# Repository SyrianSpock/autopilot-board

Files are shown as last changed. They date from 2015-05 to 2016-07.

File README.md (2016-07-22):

Speedy, the nanocopter
======================

The aim of this project is to design a board enabling the control of a small quadrotor (nanocopter) that can be tracked by external visual sensors.

### Specifications
* Cortex M4 MCU
* Four infrared LEDs on each side of the board for IR vision tracking. Each side can be controlled separately.
* Two full H bridges: one half bridge per motor to allow active braking of the motors.
* IMU:
    - MPU9250 (9 axis): accelerometer, gyroscope and magnetometer
    - MS5611 barometer
* Ground distance sensor:
    - ST VL53L0X for landing / ground approach
* Telemetry module:
    - ESP12E for telemetry and telecommand through WiFi
* USB interface (for DFU programming / serial interface) and power/charging
* Battery management unit
	- Monitor battery (current, voltage)
	- Supply power to the board from a LiPo (1S) input
	- Recharge the battery through USB

### PCB

The 40mm x 40mm board is rendered below
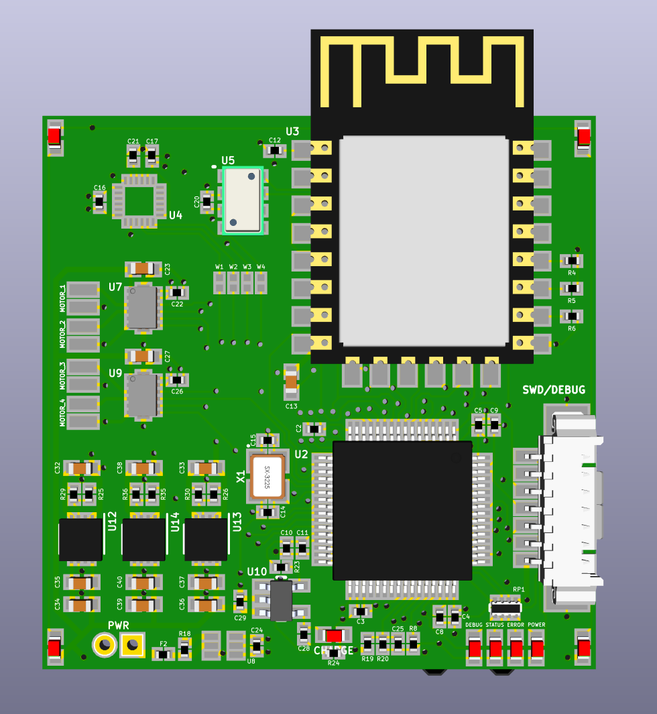
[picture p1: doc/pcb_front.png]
PCB front view

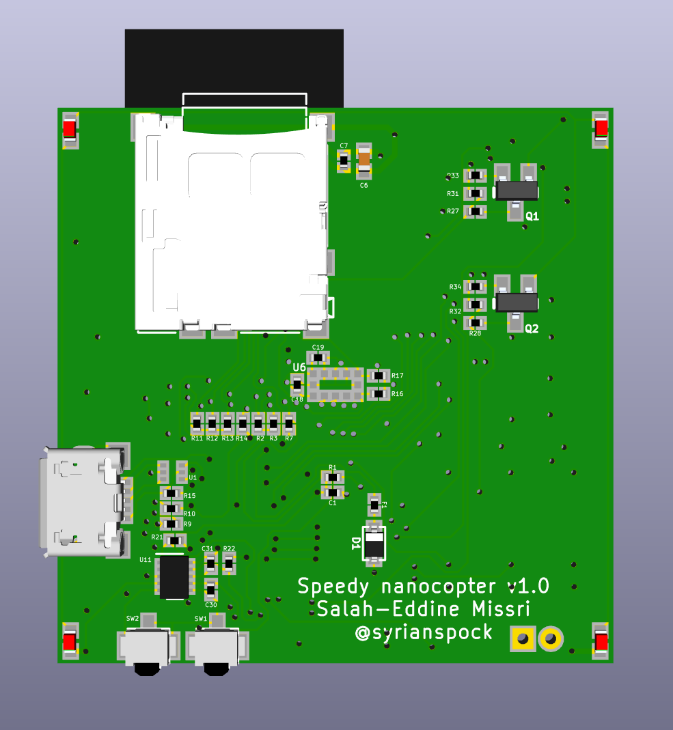
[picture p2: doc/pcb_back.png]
PCB back view


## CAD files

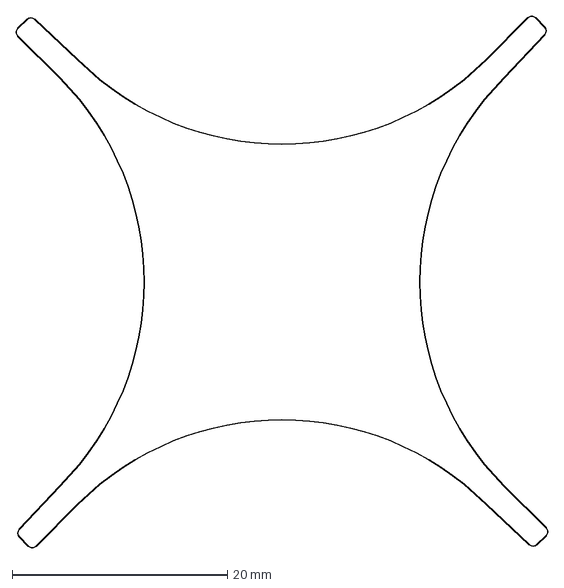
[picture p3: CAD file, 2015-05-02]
mechanics/PCB_shape.dxf
49.4 x 49.4 mm

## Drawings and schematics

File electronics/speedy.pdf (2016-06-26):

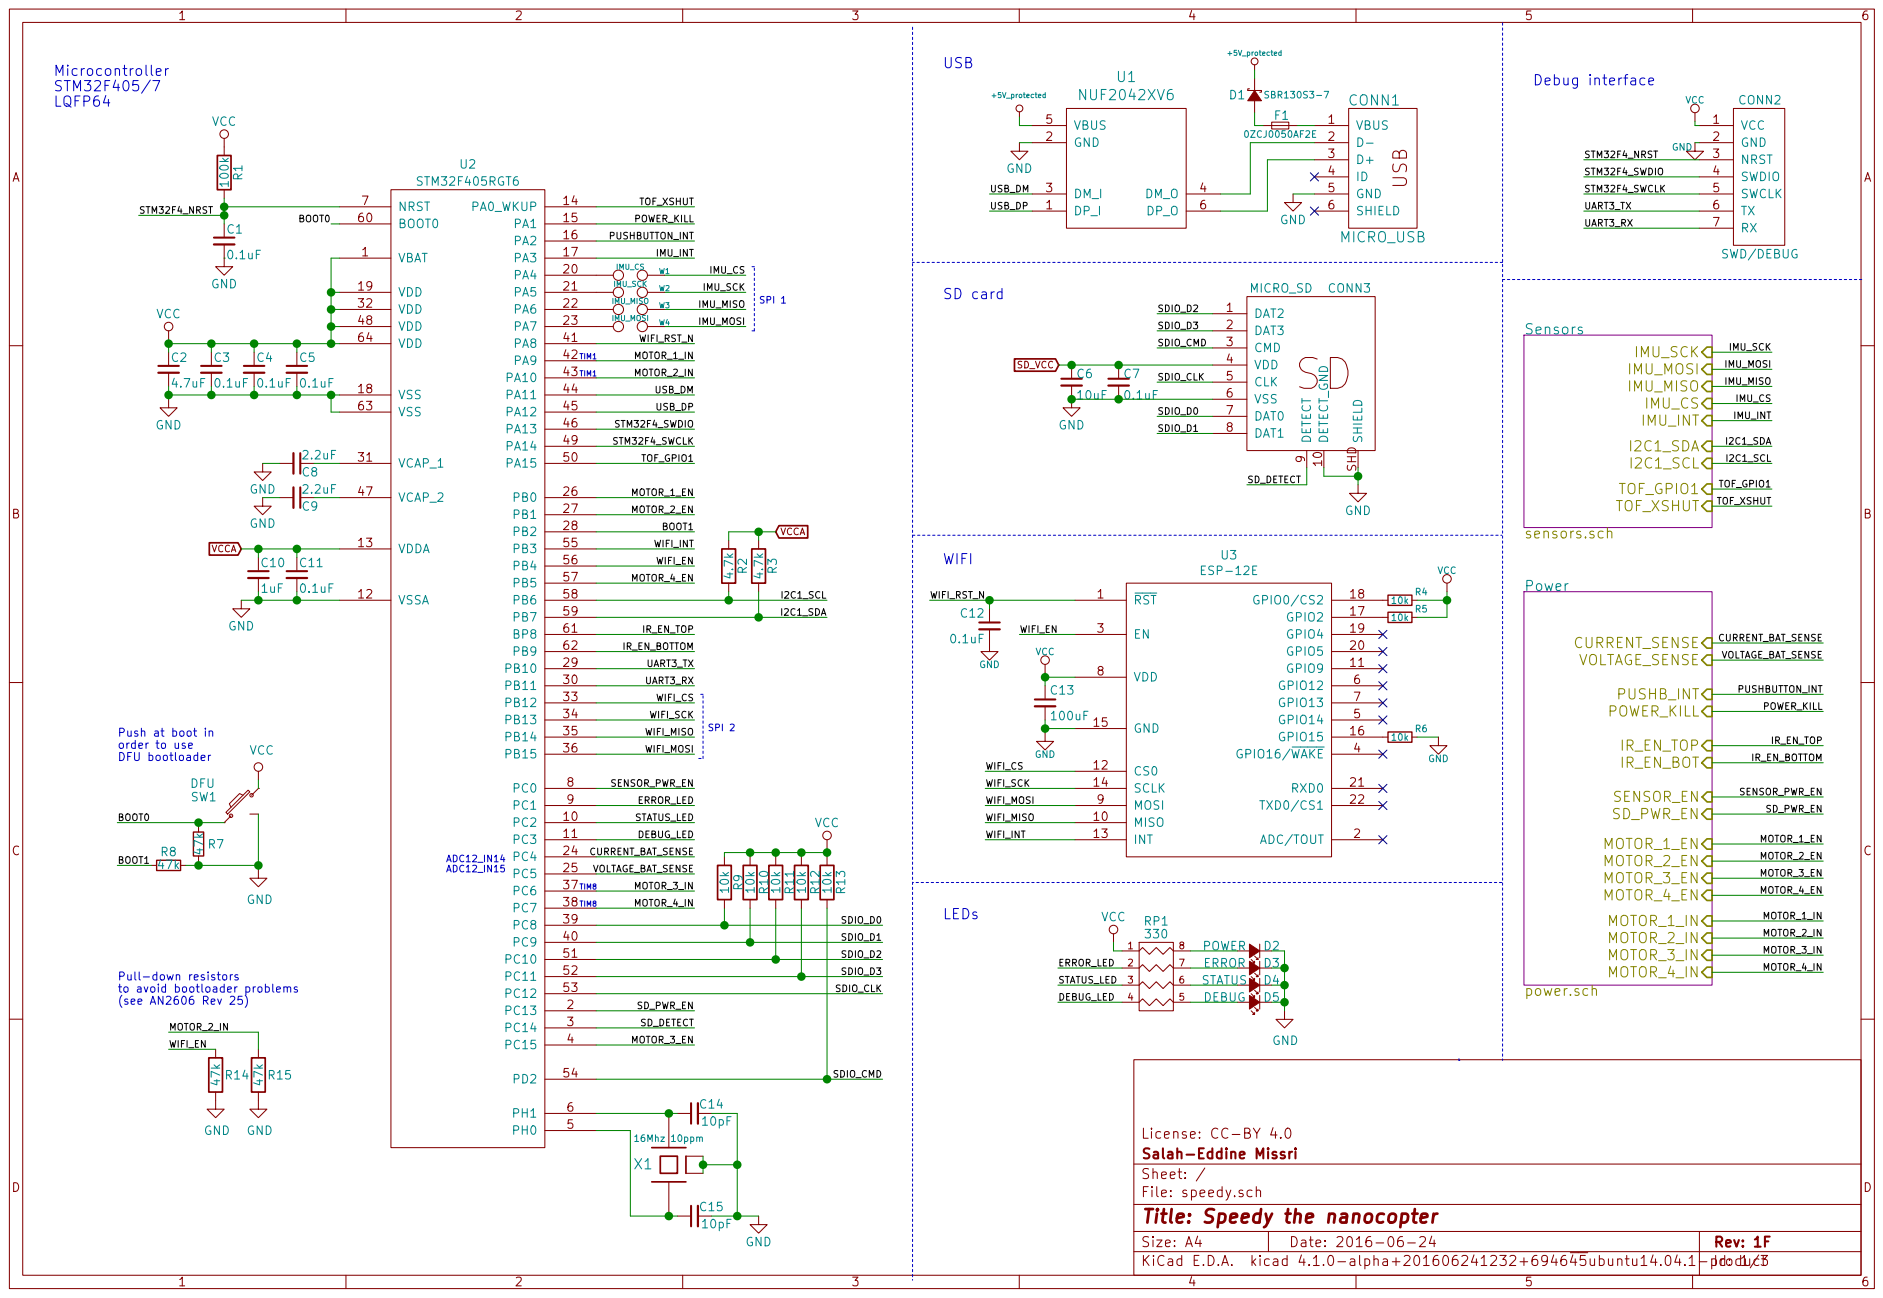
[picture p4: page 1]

Pull-down resistors
to avoid bootloader problems (see AN2606 Rev 25)

File: speedy.sch Sheet: / Salah-Eddine Missri License: CC-BY 4.0

Id: 1/3 Title: Speedy the nanocopter

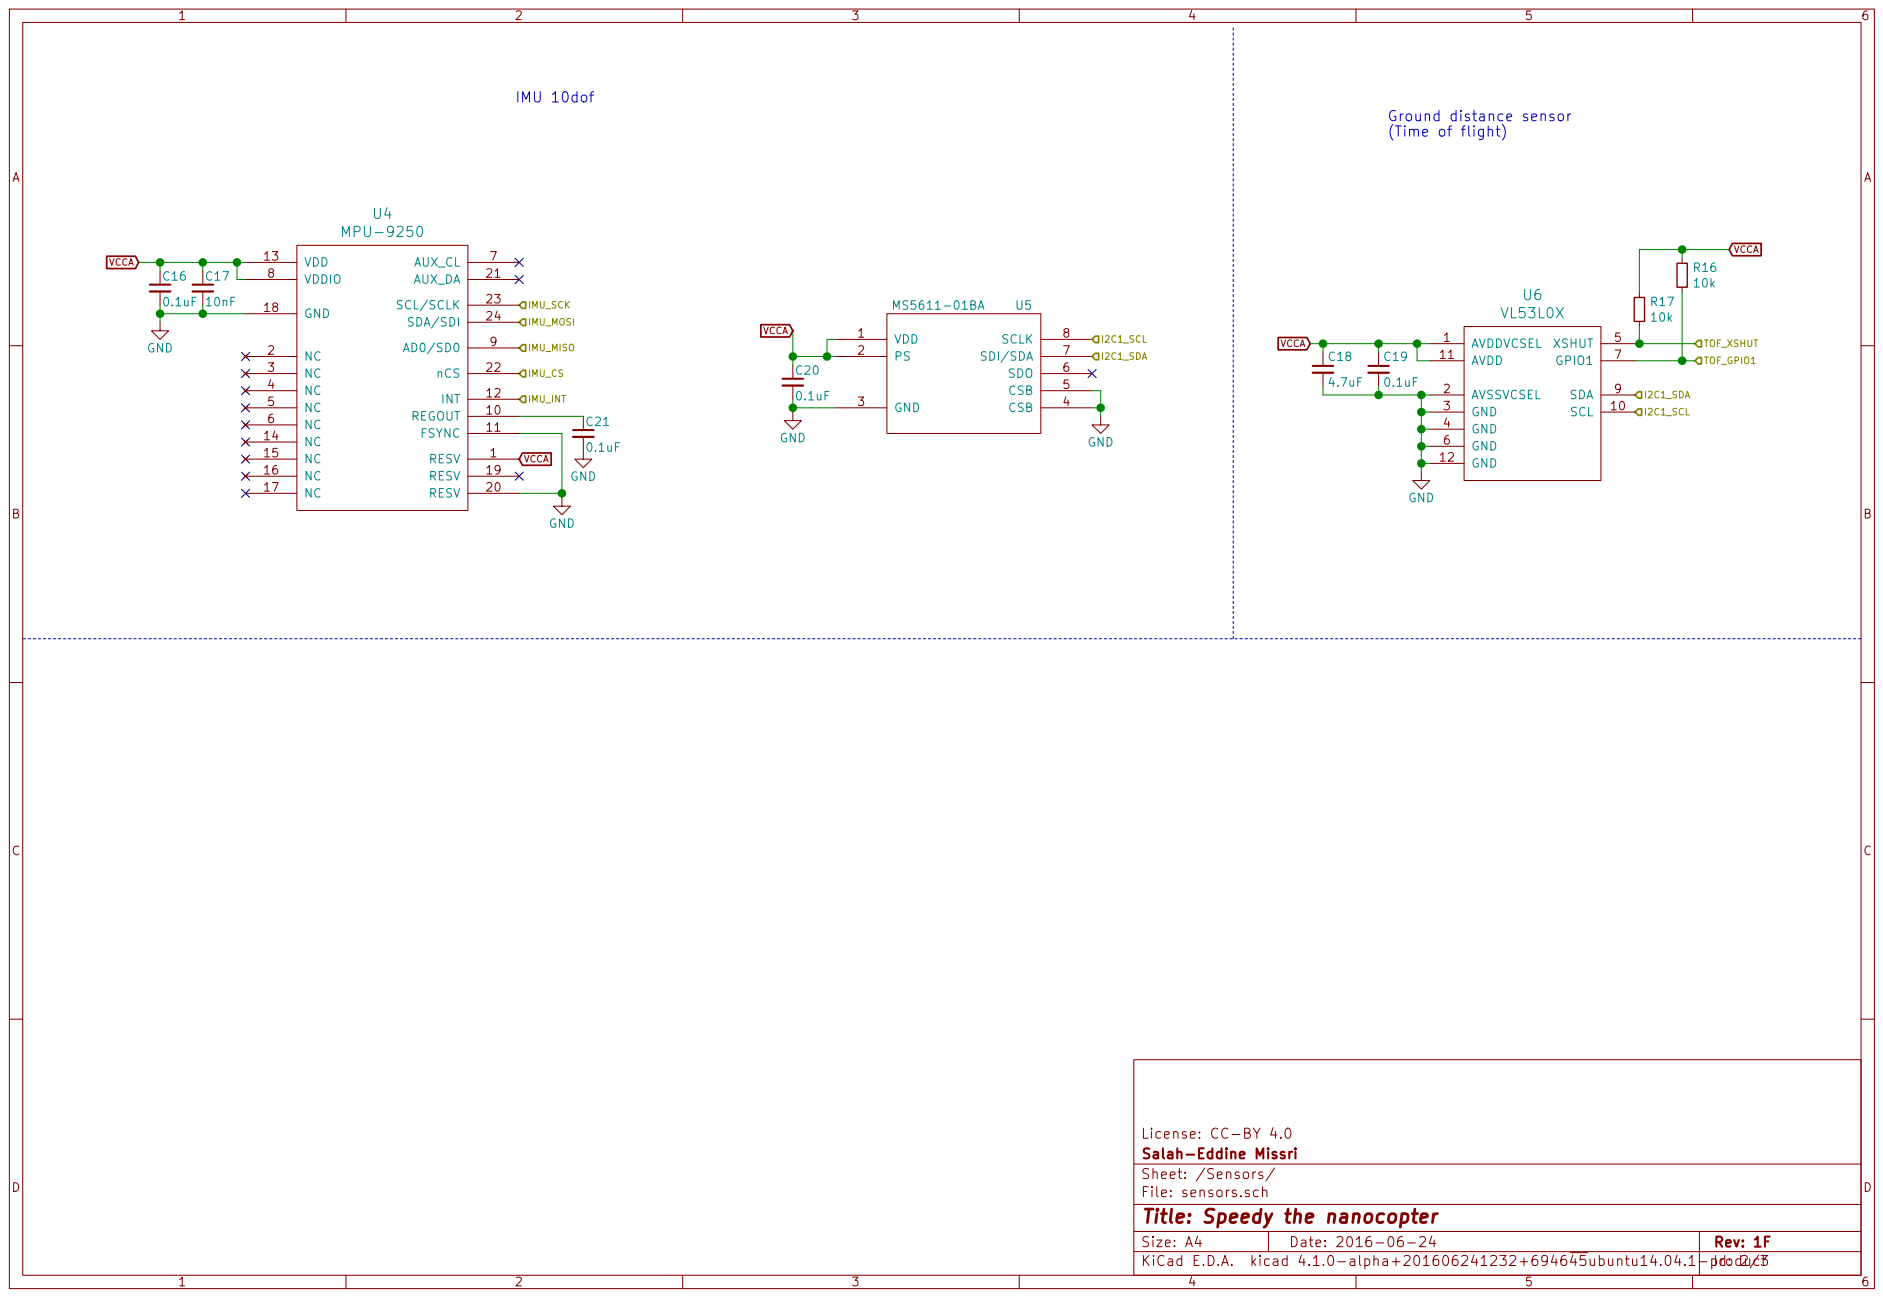
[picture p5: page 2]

Id: 2/3 Title: Speedy the nanocopter File: sensors.sch Sheet: /Sensors/ Salah-Eddine Missri License: CC-BY 4.0

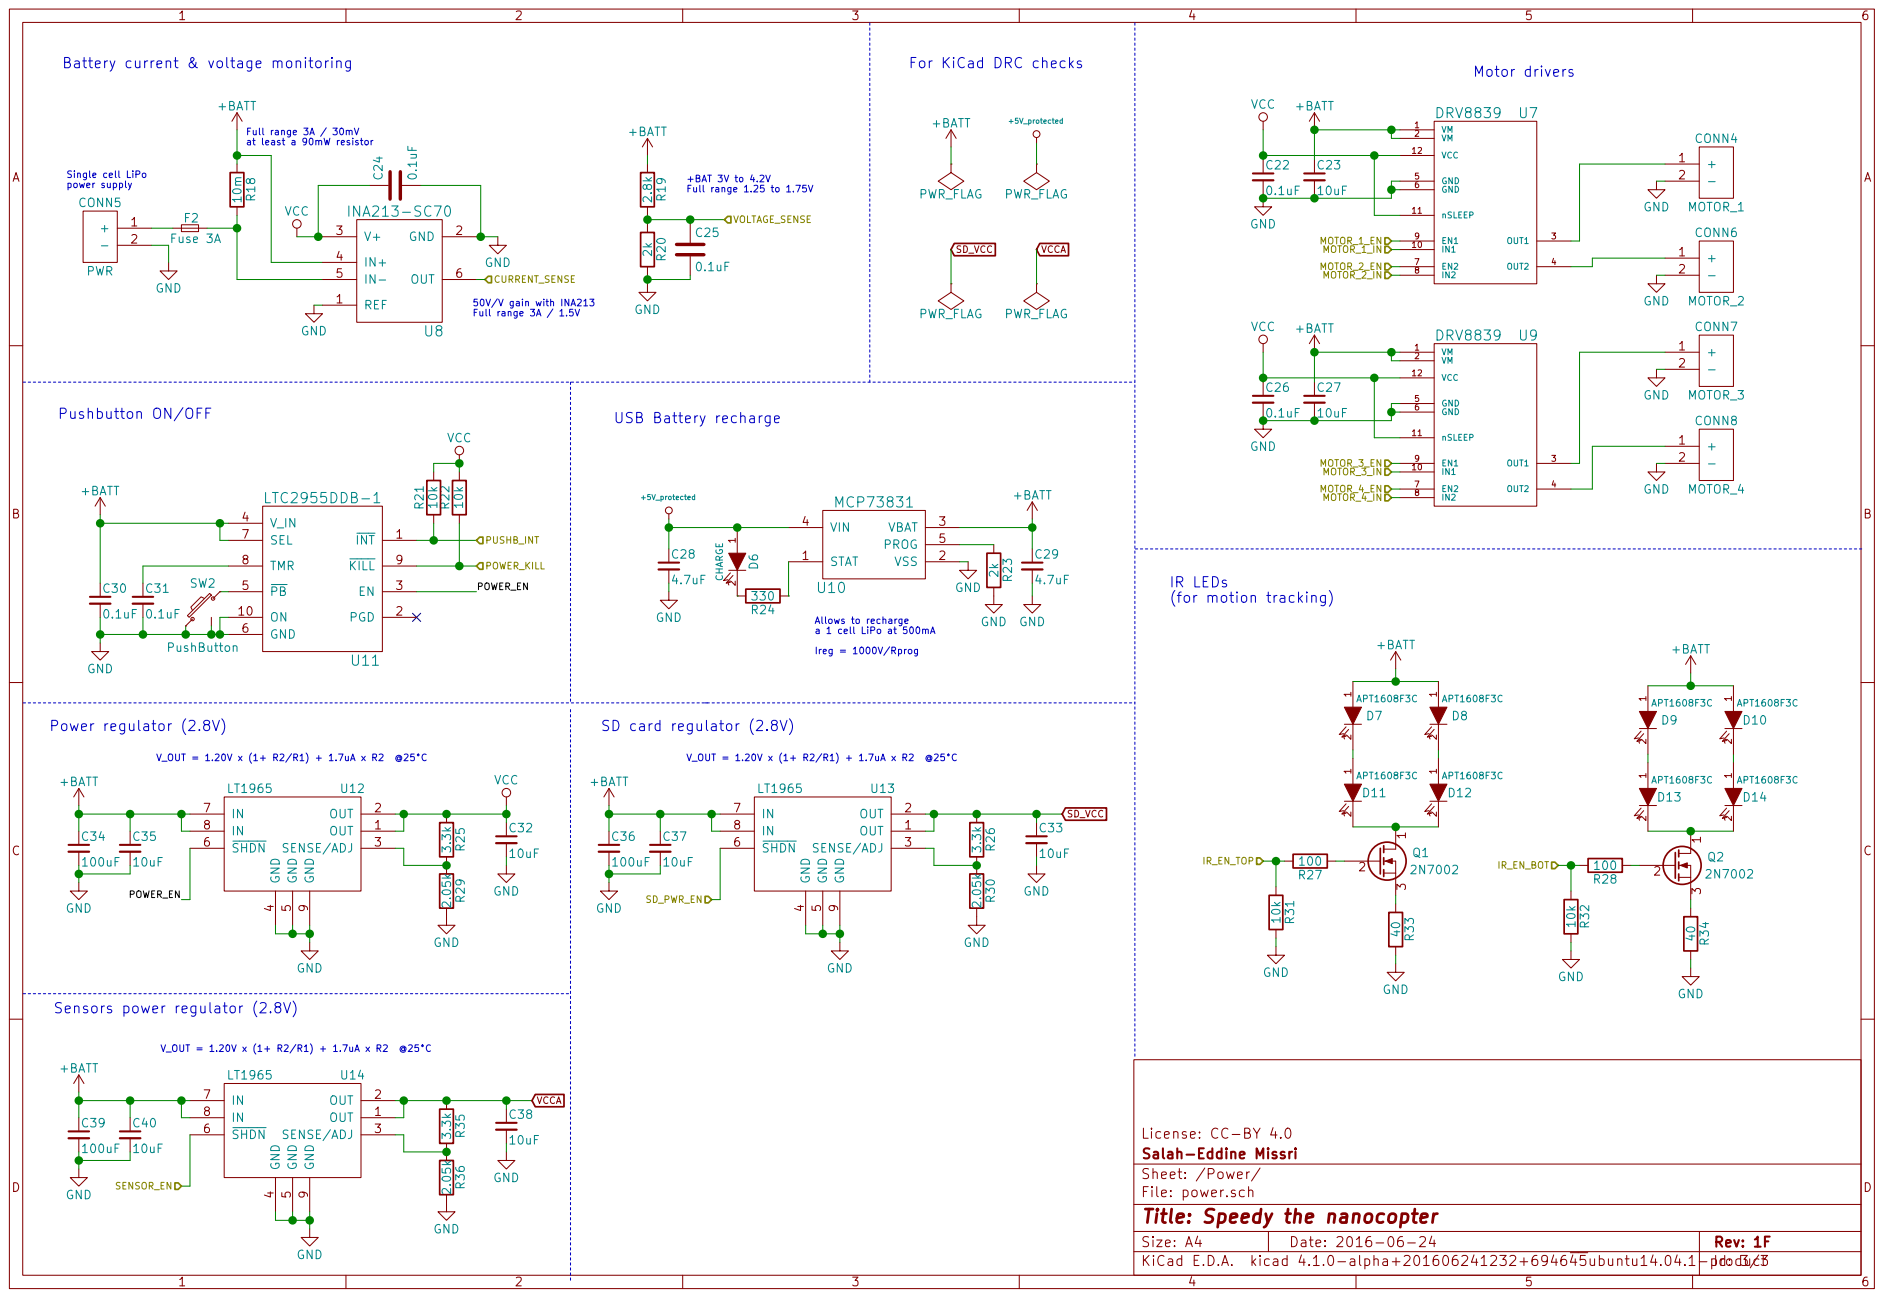
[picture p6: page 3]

Full range 1.25 to 1.75V Battery current & voltage monitoring
at least a 90mW resistor GND

For KiCad DRC checks

1 2 D6 CHARGE R23 2k Allows to recharge a 1 cell LiPo at 500mA

File: power.sch Sheet: /Power/ Salah-Eddine Missri License: CC-BY 4.0

Id: 3/3 Title: Speedy the nanocopter

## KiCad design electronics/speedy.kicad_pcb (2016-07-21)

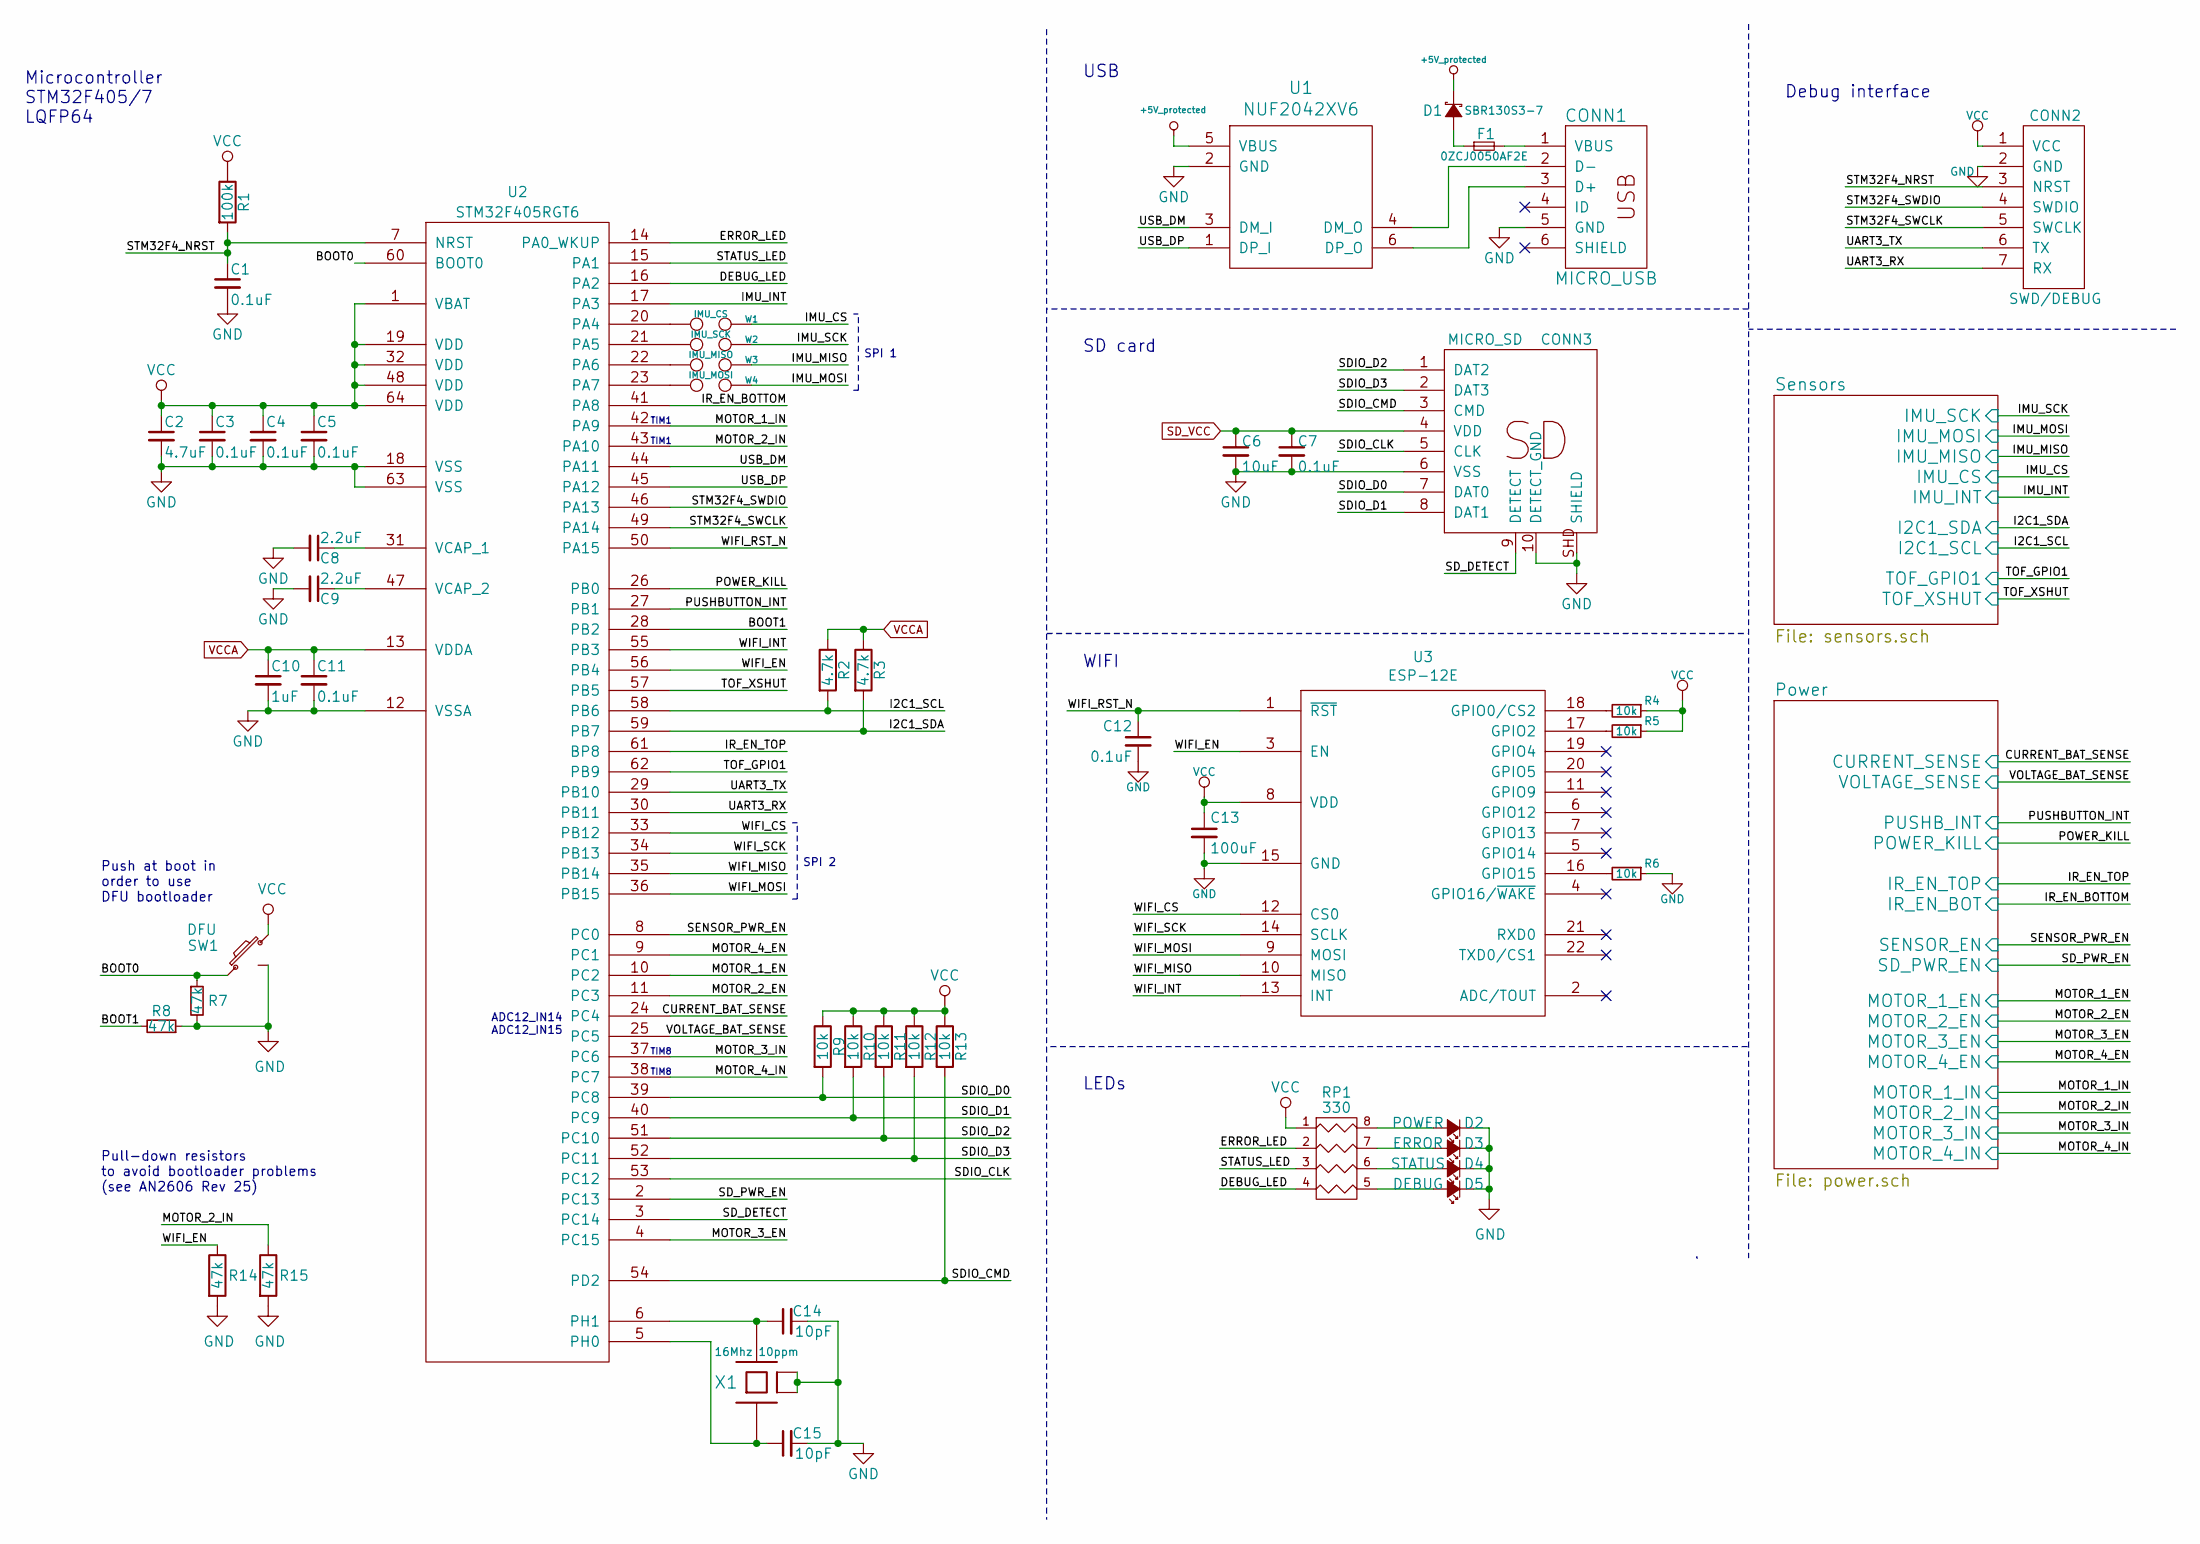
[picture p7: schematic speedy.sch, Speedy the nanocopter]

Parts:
C1, C3, C4, C5, C7, C11, C12: 0.1uF; _0402
C2: 4.7uF; _0402
C6: 10uF; C_0603
C8, C9: 2.2uF; _0402
C10: 1uF; _0402
C13: 100uF; C_0603
C14, C15: 10pF; _0402
CONN1: MICRO_USB; _Micro-USB-AB-receptacle-SMT-th
CONN2: SWD/DEBUG; _Molex-PicoBlade-SMD-7
CONN3: MICRO_SD; _Molex-microSD-502570-0893
D1: SBR130S3-7; _SOD-323
D2: POWER; D_0603
D3: ERROR; D_0603
D4: STATUS; D_0603
D5: DEBUG; D_0603
F1: 0ZCJ0050AF2E; _0402
R1: 100k; _0402
R2, R3: 4.7k; _0402
R4, R5, R6, R9, R10, R11, R12, R13: 10k; _0402
R7, R8, R14, R15: 47k; _0402
RP1: 330; R_Array_Concave_4x0402
SW1: DFU; SMD_Pushbutton_B3U-3100P
U1: NUF2042XV6; SOT-563_6-lead
U2: STM32F405RGT6; _LQFP64
U3: ESP-12E; ESP-12-E
W1: IMU_CS; TestPad
W2: IMU_SCK; TestPad
W3: IMU_MISO; TestPad
W4: IMU_MOSI; TestPad
X1: 16Mhz 10ppm; _TSX-3225-SMD-XTAL

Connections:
+5V_protected: D1.2 (C), U1.5 (VBUS); also elsewhere on the board
/BOOT0: R7.1, SW1.1, U2.60 (BOOT0)
/BOOT1: R8.2, U2.28 (PB2)
/CURRENT_BAT_SENSE: U2.24 (PC4); also elsewhere on the board
/DEBUG_LED: RP1.4, U2.16 (PA2)
/ERROR_LED: RP1.2, U2.14 (PA0_WKUP)
/I2C1_SCL: R2.2, U2.58 (PB6); also elsewhere on the board
/I2C1_SDA: R3.2, U2.59 (PB7); also elsewhere on the board
/IMU_CS: W1.2; also elsewhere on the board
/IMU_INT: U2.17 (PA3); also elsewhere on the board
/IMU_MISO: W3.2; also elsewhere on the board
/IMU_MOSI: W4.2; also elsewhere on the board
/IMU_SCK: W2.2; also elsewhere on the board
/IR_EN_BOTTOM: U2.41 (PA8); also elsewhere on the board
/IR_EN_TOP: U2.61 (BP8); also elsewhere on the board
/MOTOR_1_EN: U2.10 (PC2); also elsewhere on the board
/MOTOR_1_IN: U2.42 (PA9); also elsewhere on the board
/MOTOR_2_EN: U2.11 (PC3); also elsewhere on the board
/MOTOR_2_IN: R15.1, U2.43 (PA10); also elsewhere on the board
/MOTOR_3_EN: U2.4 (PC15); also elsewhere on the board
/MOTOR_3_IN: U2.37 (PC6); also elsewhere on the board
/MOTOR_4_EN: U2.9 (PC1); also elsewhere on the board
/MOTOR_4_IN: U2.38 (PC7); also elsewhere on the board
/POWER_KILL: U2.26 (PB0); also elsewhere on the board
/PUSHBUTTON_INT: U2.27 (PB1); also elsewhere on the board
/SDIO_CLK: CONN3.5 (CLK), U2.53 (PC12)
/SDIO_CMD: CONN3.3 (CMD), R13.2, U2.54 (PD2)
/SDIO_D0: CONN3.7 (DAT0), R9.2, U2.39 (PC8)
/SDIO_D1: CONN3.8 (DAT1), R10.2, U2.40 (PC9)
/SDIO_D2: CONN3.1 (DAT2), R11.2, U2.51 (PC10)
/SDIO_D3: CONN3.2 (DAT3), R12.2, U2.52 (PC11)
/SD_DETECT: CONN3.9 (DETECT), U2.3 (PC14)
/SD_PWR_EN: U2.2 (PC13); also elsewhere on the board
/SENSOR_PWR_EN: U2.8 (PC0); also elsewhere on the board
/STATUS_LED: RP1.3, U2.15 (PA1)
/STM32F4_NRST: C1.1, CONN2.3 (NRST), R1.2, U2.7 (NRST)
/STM32F4_SWCLK: CONN2.5 (SWCLK), U2.49 (PA14)
/STM32F4_SWDIO: CONN2.4 (SWDIO), U2.46 (PA13)
/TOF_GPIO1: U2.62 (PB9); also elsewhere on the board
/TOF_XSHUT: U2.57 (PB5); also elsewhere on the board
/UART3_RX: CONN2.7 (RX), U2.30 (PB11)
/UART3_TX: CONN2.6 (TX), U2.29 (PB10)
/USB_DM: U1.3 (DM_I), U2.44 (PA11)
/USB_DP: U1.1 (DP_I), U2.45 (PA12)
/VOLTAGE_BAT_SENSE: U2.25 (PC5); also elsewhere on the board
/WIFI_CS: U2.33 (PB12), U3.12 (CS0)
/WIFI_EN: R14.1, U2.56 (PB4), U3.3 (EN)
/WIFI_INT: U2.55 (PB3), U3.13 (INT)
/WIFI_MISO: U2.35 (PB14), U3.10 (MISO)
/WIFI_MOSI: U2.36 (PB15), U3.9 (MOSI)
/WIFI_RST_N: C12.1, U2.50 (PA15), U3.1 (~RST)
/WIFI_SCK: U2.34 (PB13), U3.14 (SCLK)
GND: C1.2, C2.2, C3.2, C4.2, C5.2, C6.2, C7.2, C8.2, C9.2, C10.2, C11.2, C12.2, C13.2, C14.2, C15.2, CONN1.5 (GND), CONN2.2 (GND), CONN2.MECH (GND), CONN3.6 (VSS), CONN3.10 (DETECT_GND), CONN3.SHD (SHIELD), D2.1 (K), D3.1 (K), D4.1 (K), D5.1 (K), R6.1, R7.2, R8.1, R14.2, R15.2, SW1.3 (GND), U1.2 (GND), U2.12 (VSSA), U2.18 (VSS), U2.63 (VSS), U3.15 (GND), X1.2 (case), X1.4 (case); also elsewhere on the board
unnamed: C8.1, U2.31 (VCAP_1)
unnamed: C9.1, U2.47 (VCAP_2)
unnamed: C14.1, U2.6 (PH1), X1.3
unnamed: C15.1, U2.5 (PH0), X1.1
unnamed: CONN1.1 (VBUS), F1.2
unnamed: CONN1.2 (D-), U1.4 (DM_O)
unnamed: CONN1.3 (D+), U1.6 (DP_O)
unnamed: D1.1 (A), F1.1
unnamed: D2.2 (A), RP1.8 (R1)
unnamed: D3.2 (A), RP1.7 (R2)
unnamed: D4.2 (A), RP1.6 (R3)
unnamed: D5.2 (A), RP1.5 (R4)
unnamed: R4.2, U3.18 (GPIO0/CS2)
unnamed: R5.2, U3.17 (GPIO2)
unnamed: R6.2, U3.16 (GPIO15)
unnamed: U2.20 (PA4), W1.1
unnamed: U2.21 (PA5), W2.1
unnamed: U2.22 (PA6), W3.1
unnamed: U2.23 (PA7), W4.1
SD_VCC: C6.1, C7.1, CONN3.4 (VDD); also elsewhere on the board
VCC: C2.1, C3.1, C4.1, C5.1, C13.1, CONN2.1 (VCC), R1.1, R4.1, R5.1, R9.1, R10.1, R11.1, R12.1, R13.1, RP1.1, SW1.2, U2.1 (VBAT), U2.19 (VDD), U2.32 (VDD), U2.48 (VDD), U2.64 (VDD), U3.8 (VDD); also elsewhere on the board
VCCA: C10.1, C11.1, R2.1, R3.1, U2.13 (VDDA); also elsewhere on the board

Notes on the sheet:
SPI 2
ADC12_IN14 ADC12_IN15
Microcontroller STM32F405/7 LQFP64
SD card
Debug interface
USB
LEDs
Push at boot in order to use DFU bootloader
TIM8
TIM1
Pull-down resistors to avoid bootloader problems (see AN2606 Rev 25)
SPI 1
WIFI

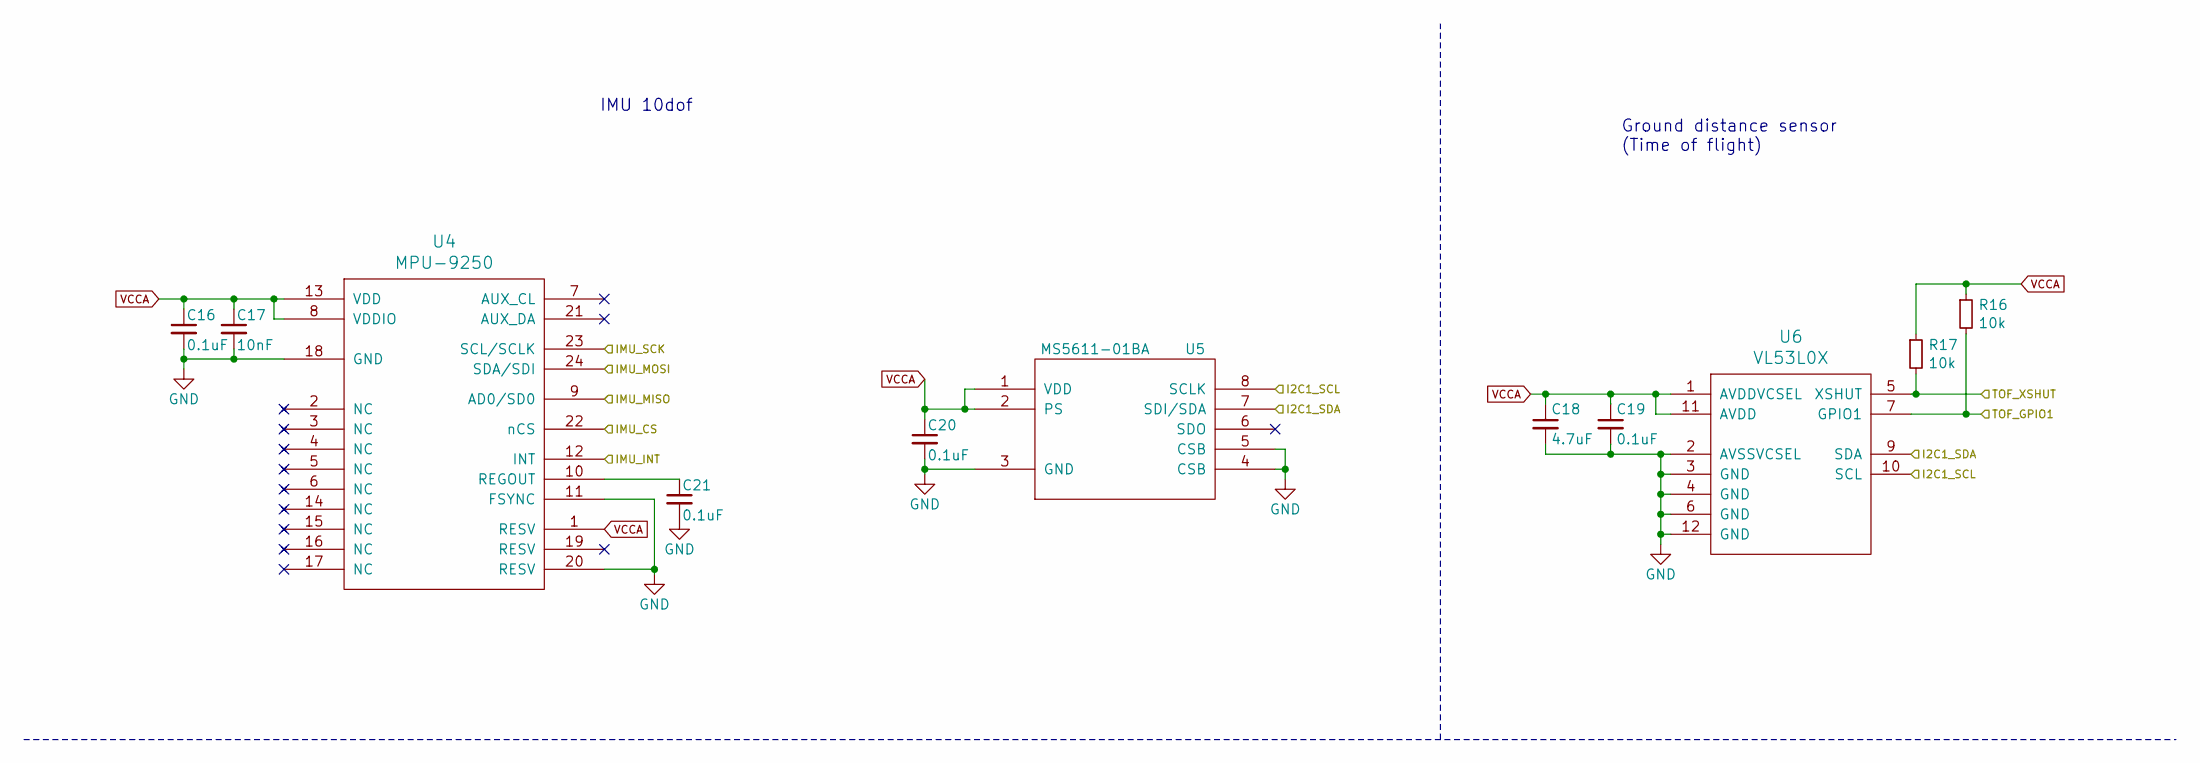
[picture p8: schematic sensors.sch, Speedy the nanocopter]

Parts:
C16, C19, C20, C21: 0.1uF; _0402
C17: 10nF; _0402
C18: 4.7uF; _0402
R16, R17: 10k; _0402
U4: MPU-9250; _MPU-9XX0
U5: MS5611-01BA; _MS5611-01BA
U6: VL53L0X; ST-VL53L0X

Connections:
/I2C1_SCL: U5.8 (SCLK), U6.10 (SCL); also elsewhere on the board
/I2C1_SDA: U5.7 (SDI/SDA), U6.9 (SDA); also elsewhere on the board
/IMU_CS: U4.22 (nCS); also elsewhere on the board
/IMU_INT: U4.12 (INT); also elsewhere on the board
/IMU_MISO: U4.9 (AD0/SD0); also elsewhere on the board
/IMU_MOSI: U4.24 (SDA/SDI); also elsewhere on the board
/IMU_SCK: U4.23 (SCL/SCLK); also elsewhere on the board
/TOF_GPIO1: R16.2, U6.7 (GPIO1); also elsewhere on the board
/TOF_XSHUT: R17.2, U6.5 (XSHUT); also elsewhere on the board
GND: C16.2, C17.2, C18.2, C19.2, C20.2, C21.2, U4.11 (FSYNC), U4.18 (GND), U4.20 (RESV), U5.3 (GND), U5.4 (CSB), U5.5 (CSB), U6.2 (AVSSVCSEL), U6.3 (GND), U6.4 (GND), U6.6 (GND), U6.12 (GND); also elsewhere on the board
unnamed: C21.1, U4.10 (REGOUT)
VCCA: C16.1, C17.1, C18.1, C19.1, C20.1, R16.1, R17.1, U4.1 (RESV), U4.8 (VDDIO), U4.13 (VDD), U5.1 (VDD), U5.2 (PS), U6.1 (AVDDVCSEL), U6.11 (AVDD); also elsewhere on the board

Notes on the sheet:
Ground distance sensor (Time of flight)
IMU 10dof

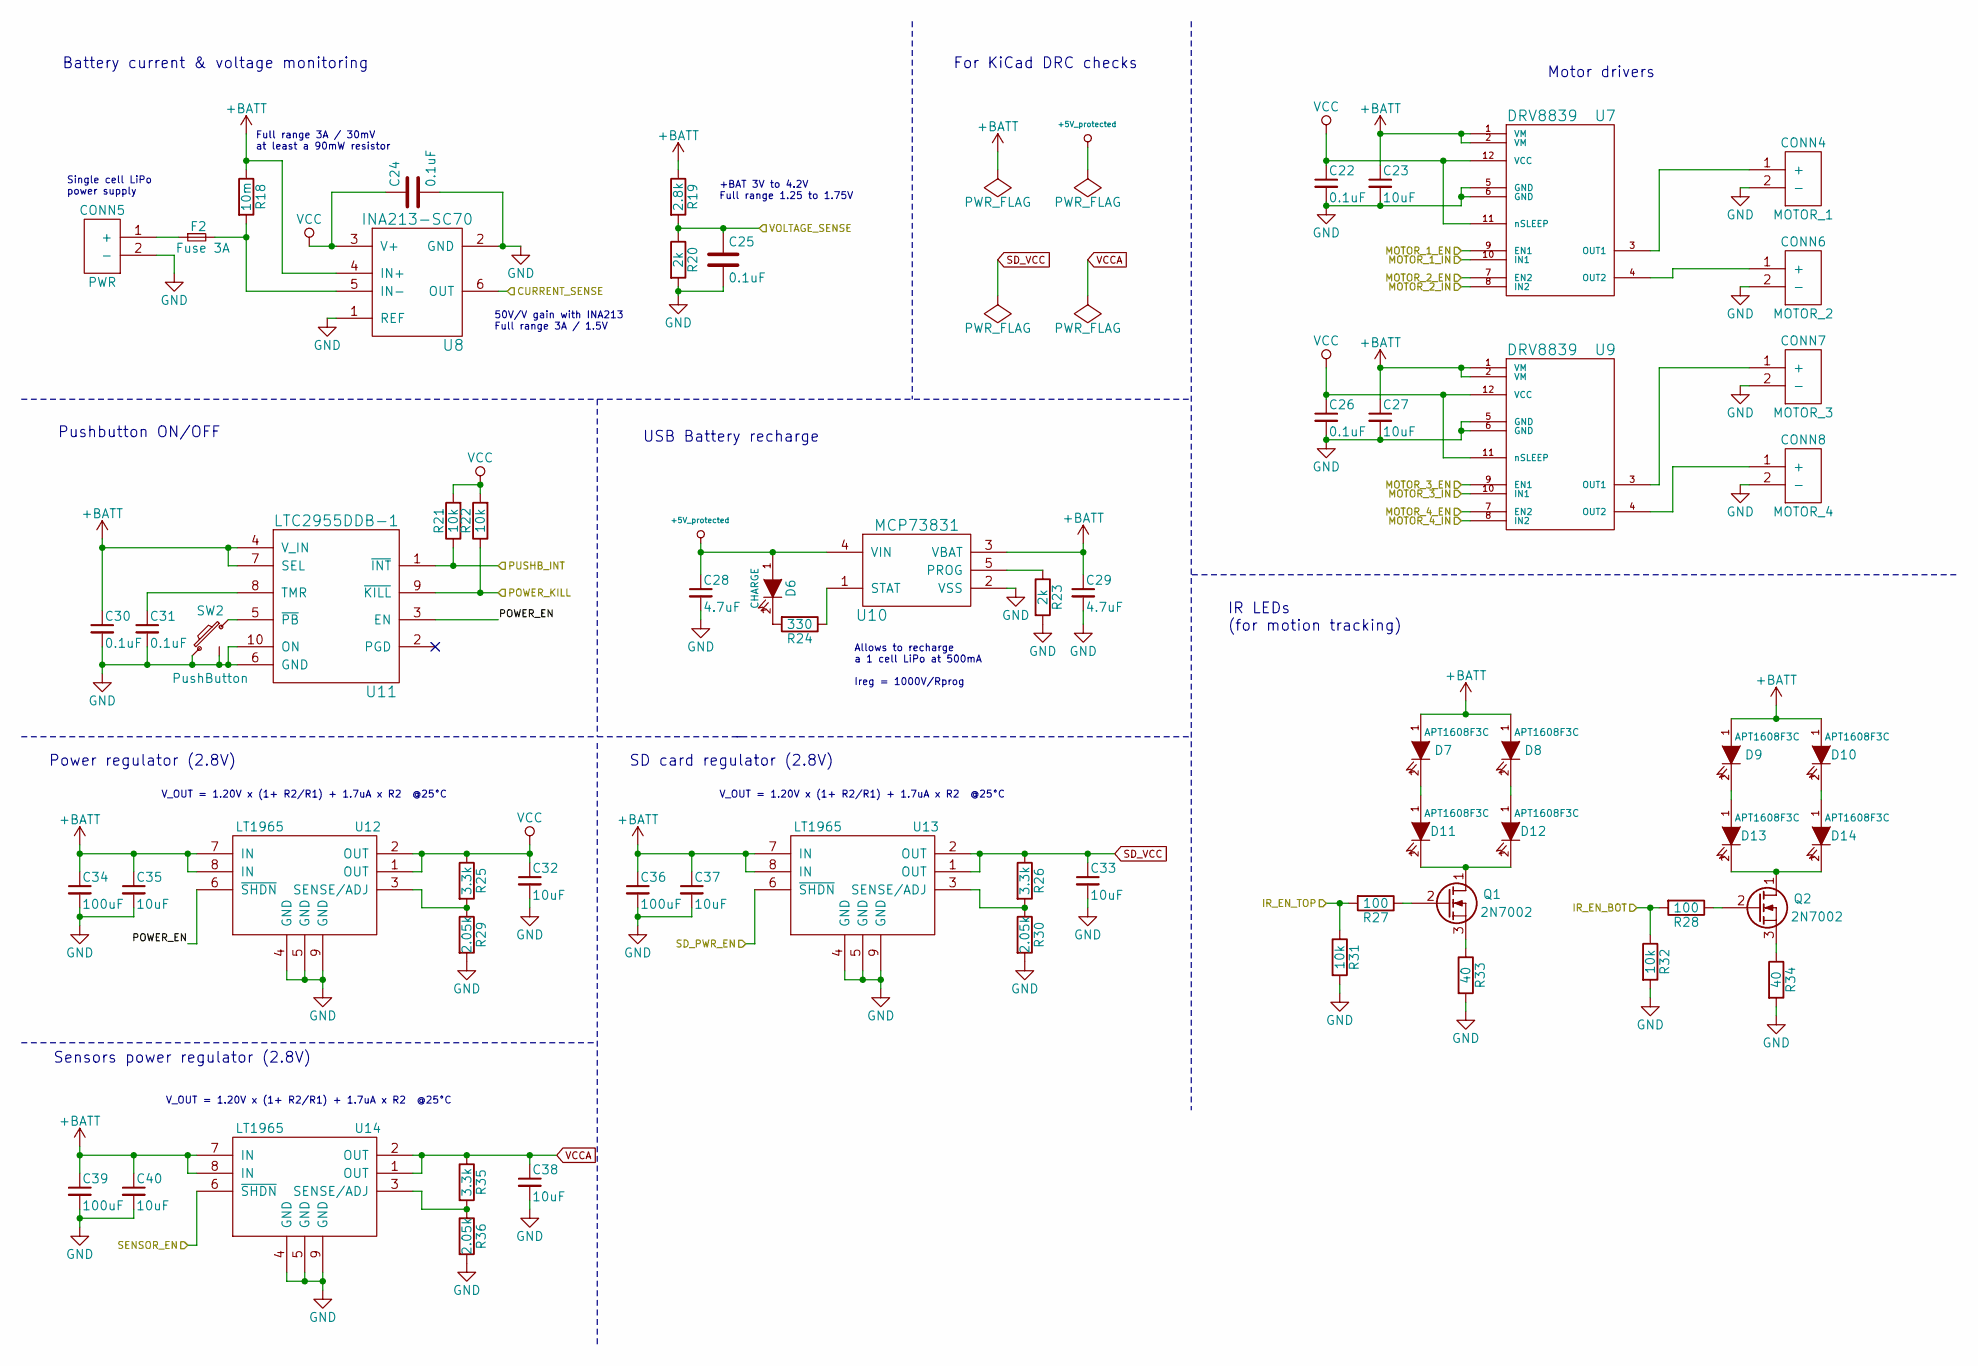
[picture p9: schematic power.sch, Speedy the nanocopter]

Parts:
C22, C24, C25, C26, C30, C31: 0.1uF; _0402
C23, C27, C32, C33, C35, C37, C38, C40: 10uF; C_0603
C28, C29: 4.7uF; _0402
C34, C36, C39: 100uF; C_0603
CONN4: MOTOR_1; _Solder_Pad1.27_2
CONN5: PWR; _Pin2mm_2
CONN6: MOTOR_2; _Solder_Pad1.27_2
CONN7: MOTOR_3; _Solder_Pad1.27_2
CONN8: MOTOR_4; _Solder_Pad1.27_2
D6: CHARGE; D_0603
D7, D8, D9, D10, D11, D12, D13, D14: APT1608F3C; D_0603
F2: Fuse 3A; _0402
Q1, Q2: 2N7002; _SOT23-3
R18: 10m; _0402
R19: 2.8k; _0402
R20, R23: 2k; _0402
R21, R22, R31, R32: 10k; _0402
R24: 330; _0402
R25, R26, R35: 3.3k; _0402
R27, R28: 100; _0402
R29, R30, R36: 2.05k; _0402
R33, R34: 40; _0402
SW2: PushButton; SMD_Pushbutton_B3U-3100P
U7, U9: DRV8839; TI-DRV8839_PWSON-N12
U8: INA213-SC70; SC70
U10: MCP73831; _TSOT23-5
U11: LTC2955DDB-1; DFN-10-1EP_2x3mm_Pitch0.5mm
U12, U13, U14: LT1965; DFN-8-1EP_3x3mm_Pitch0.5mm

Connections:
+5V_protected: C28.1, D6.1 (A), U10.4 (VIN); also elsewhere on the board
+BATT: C23.1, C27.1, C29.1, C30.1, C34.1, C35.1, C36.1, C37.1, C39.1, C40.1, D7.1 (A), D8.1 (A), D9.1 (A), D10.1 (A), R18.1, R19.1, U7.1 (VM), U7.2 (VM), U8.4 (IN+), U9.1 (VM), U9.2 (VM), U10.3 (VBAT), U11.4 (V_IN), U11.7 (SEL), U12.7 (IN), U12.8 (IN), U13.7 (IN), U13.8 (IN), U14.7 (IN), U14.8 (IN)
/CURRENT_BAT_SENSE: U8.6 (OUT); also elsewhere on the board
/IR_EN_BOTTOM: R28.2, R32.1; also elsewhere on the board
/IR_EN_TOP: R27.2, R31.1; also elsewhere on the board
/MOTOR_1_EN: U7.9 (EN1); also elsewhere on the board
/MOTOR_1_IN: U7.10 (IN1); also elsewhere on the board
/MOTOR_2_EN: U7.7 (EN2); also elsewhere on the board
/MOTOR_2_IN: U7.8 (IN2); also elsewhere on the board
/MOTOR_3_EN: U9.9 (EN1); also elsewhere on the board
/MOTOR_3_IN: U9.10 (IN1); also elsewhere on the board
/MOTOR_4_EN: U9.7 (EN2); also elsewhere on the board
/MOTOR_4_IN: U9.8 (IN2); also elsewhere on the board
/POWER_KILL: R22.1, U11.9 (~KILL); also elsewhere on the board
/PUSHBUTTON_INT: R21.1, U11.1 (~INT); also elsewhere on the board
/Power/POWER_EN: U11.3 (EN), U12.6 (~SHDN)
/SD_PWR_EN: U13.6 (~SHDN); also elsewhere on the board
/SENSOR_PWR_EN: U14.6 (~SHDN); also elsewhere on the board
/VOLTAGE_BAT_SENSE: C25.1, R19.2, R20.1; also elsewhere on the board
GND: C22.2, C23.2, C24.2, C25.2, C26.2, C27.2, C28.2, C29.2, C30.2, C31.2, C32.2, C33.2, C34.2, C35.2, C36.2, C37.2, C38.2, C39.2, C40.2, CONN4.2 (-), CONN5.2 (-), CONN6.2 (-), CONN7.2 (-), CONN8.2 (-), R20.2, R23.2, R29.2, R30.2, R31.2, R32.2, R33.2, R34.2, R36.2, SW2.2, SW2.3 (GND), U7.5 (GND), U7.6 (GND), U7.THRM, U8.1 (REF), U8.2 (GND), U9.5 (GND), U9.6 (GND), U9.THRM, U10.2 (VSS), U11.6 (GND), U11.10 (ON), U12.4 (GND), U12.5 (GND), U12.9 (GND), U13.4 (GND), U13.5 (GND), U13.9 (GND), U14.4 (GND), U14.5 (GND), U14.9 (GND); also elsewhere on the board
unnamed: C31.1, U11.8 (TMR)
unnamed: CONN4.1 (+), U7.3 (OUT1)
unnamed: CONN5.1 (+), F2.1
unnamed: CONN6.1 (+), U7.4 (OUT2)
unnamed: CONN7.1 (+), U9.3 (OUT1)
unnamed: CONN8.1 (+), U9.4 (OUT2)
unnamed: D6.2 (K), R24.2
unnamed: D10.2 (K), D14.1 (A)
unnamed: D7.2 (K), D11.1 (A)
unnamed: D11.2 (K), D12.2 (K), Q1.1 (D)
unnamed: D8.2 (K), D12.1 (A)
unnamed: D9.2 (K), D13.1 (A)
unnamed: D13.2 (K), D14.2 (K), Q2.1 (D)
unnamed: F2.2, R18.2, U8.5 (IN-)
unnamed: Q1.2 (G), R27.1
unnamed: Q1.3 (S), R33.1
unnamed: Q2.2 (G), R28.1
unnamed: Q2.3 (S), R34.1
unnamed: R23.1, U10.5 (PROG)
unnamed: R24.1, U10.1 (STAT)
unnamed: R25.2, R29.1, U12.3 (SENSE/ADJ)
unnamed: R26.2, R30.1, U13.3 (SENSE/ADJ)
unnamed: R35.2, R36.1, U14.3 (SENSE/ADJ)
unnamed: SW2.1, U11.5 (~PB)
SD_VCC: C33.1, R26.1, U13.1 (OUT), U13.2 (OUT); also elsewhere on the board
VCC: C22.1, C24.1, C26.1, C32.1, R21.2, R22.2, R25.1, U7.11 (nSLEEP), U7.12 (VCC), U8.3 (V+), U9.11 (nSLEEP), U9.12 (VCC), U12.1 (OUT), U12.2 (OUT); also elsewhere on the board
VCCA: C38.1, R35.1, U14.1 (OUT), U14.2 (OUT); also elsewhere on the board

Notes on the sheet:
Allows to recharge a 1 cell LiPo at 500mA Ireg = 1000V/Rprog
V_OUT = 1.20V x (1+ R2/R1) + 1.7uA x R2 @25°C
Single cell LiPo power supply
Full range 3A / 30mV at least a 90mW resistor
50V/V gain with INA213 Full range 3A / 1.5V
+BAT 3V to 4.2V Full range 1.25 to 1.75V
Battery current & voltage monitoring
Power regulator (2.8V)
Pushbutton ON/OFF
USB Battery recharge
Motor drivers
IR LEDs (for motion tracking)
For KiCad DRC checks
Sensors power regulator (2.8V)
SD card regulator (2.8V)

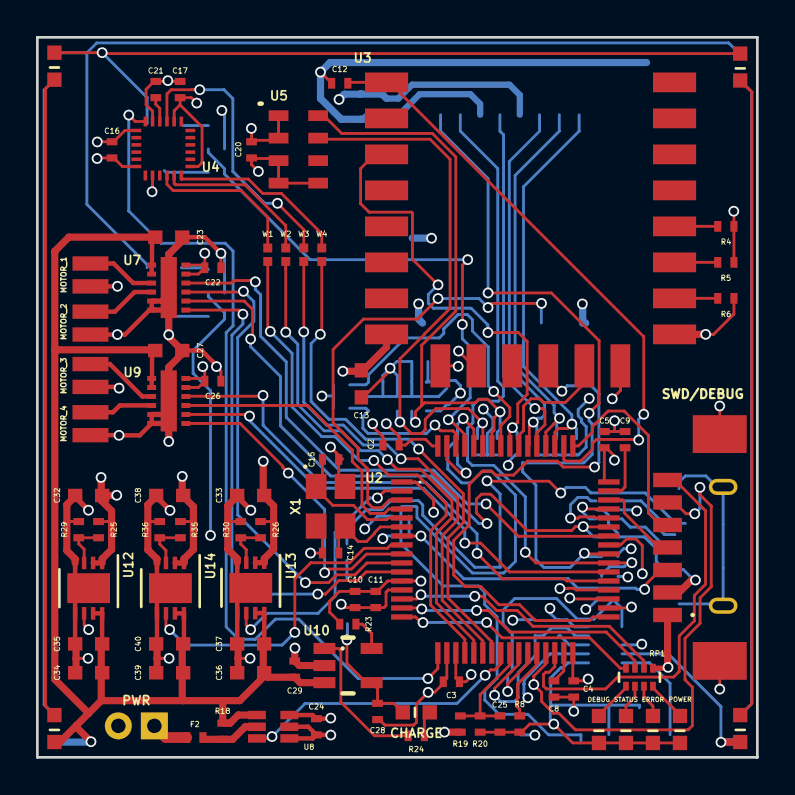
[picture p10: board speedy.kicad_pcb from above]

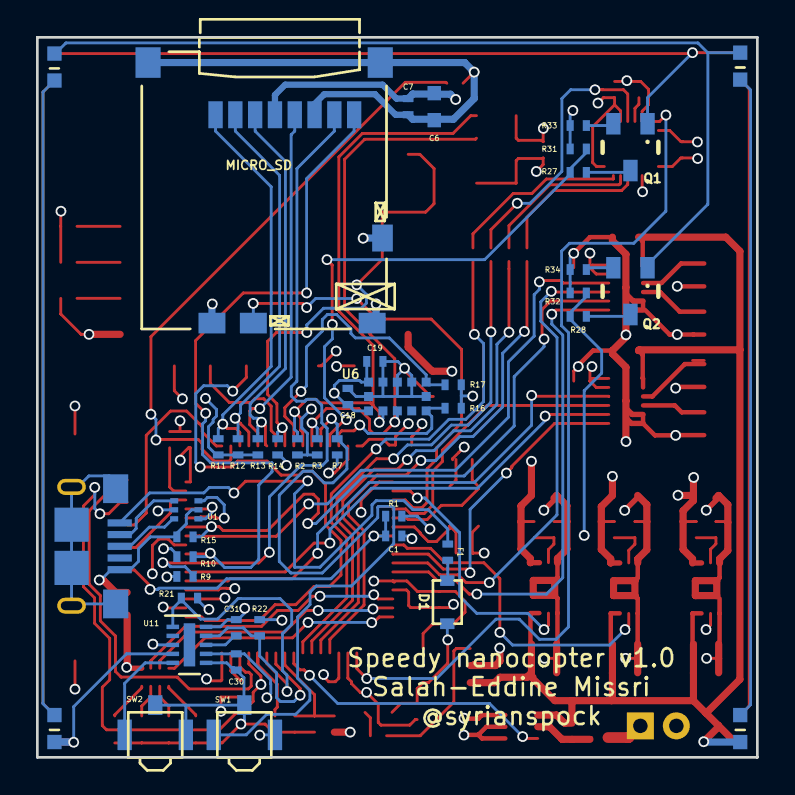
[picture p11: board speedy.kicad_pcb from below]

Board: 4 copper layers, 40.0 x 40.0 mm, 124 parts (43 on the bottom side), 102 nets.

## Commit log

2015-03-24 Add Kicad library as submodule
2015-03-26 Remove camera from autopilot board
2015-04-17 Add PCB shape
    [PCB_shape.dxf]
2015-04-21 Add STM32F4 MCU to schematics
    [speedy.sch]
2015-04-21 Add oscillator
    [speedy.sch]
2015-04-21 Add MPU 9250
    [sensors.sch, speedy.sch]
2015-04-21 Adjust MPU9250 wiring to MCU
    [sensors.sch, speedy.sch]
2015-04-21 Add ground sensor (VL6180X)
    [sensors.sch, speedy.sch]
2015-04-22 Add level shifters for i2c of TOF sensor
    [sensors.sch, speedy.sch]
2015-04-22 Add power regulator 2.8V for VL6180 TOF sensor
    [power.sch, sensors.sch, speedy.sch]
2015-04-22 LiPo recharge circuit
    [power.sch, speedy.sch]
2015-04-22 Update schematic labels to handle hierarchical signal dependencies
    [power.sch, sensors.sch, speedy.sch]
2015-04-22 Add principal power supply
    [power.sch, sensors.sch, speedy.sch]
2015-04-22 Barometer in schematic
    [sensors.sch]
2015-04-22 uSD card added to schematics
    [speedy.sch]
2015-04-25 CAN transceiver added in schematics
    [sensors.sch, speedy.sch]
2015-04-25 Motors & drivers TI drv8839 (independent pwm) added to schematics
    [power.sch, sensors.sch, speedy.sch]
2015-04-25 Second CAN connector for daisy chain
    [speedy.sch]
2015-04-25 Connect motors to timer 1
    [speedy.sch]
2015-04-28 nRF24L01+ integrated + correct capacitors
    [power.sch, sensors.sch, speedy.sch]
2015-05-01 Move nrf24 to separate sheet and Add USB termination
    [power.sch, sensors.sch, speedy.sch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]
2015-05-01 Add pushbutton power management
    [power.sch]
2015-05-01 Add IR Leds on top and bottom with enable on MCU
    [power.sch, sensors.sch, speedy.sch]
2015-05-02 PCB outline (updated)
    [PCB_shape.dxf, speedy.kicad_pcb]
2015-05-02 Battery monitoring (voltage and current sense)
    [power.sch, sensors.sch, speedy.sch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]
2015-05-02 Add debug interface (JTAG, UART, LEDs)
    [speedy.sch]
2015-06-27 Change MCU to LQFP64 (instead of BGA)
    [power.sch, sensors.sch, speedy.sch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]
2015-06-27 Minor corrections
    Wire GPIO of VL6180X to MCU
    Remove UART4
    Change Shottky diode
    Add fuse on CAN bus power
    [power.sch, sensors.sch, speedy.sch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]
2015-06-30 Remove CAN interface
    (not useful enough, takes too much place)
    [power.sch, sensors.sch, speedy.sch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]
2015-08-10 Use JTAG instead of SWD
    [speedy.sch]
2015-09-03 Remove SD card
    [power.sch, sensors.sch, speedy.sch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]
2016-01-19 Revert "Remove SD card"
    This reverts commit 4a1918bee256f93cb8d66746410e6c192988175c.
    [power.sch, sensors.sch, speedy.sch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]
2016-01-19 Regenerate netlist & Start placing footprints
    [power.sch, sensors.sch, speedy.kicad_pcb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]
2016-01-21 Finish placing components on PCB
    [speedy.kicad_pcb, speedy.sch]
2016-01-21 Draw edge cuts
    [speedy.kicad_pcb]
2016-01-21 Update pdf schematics
2016-01-21 Checkin kicad pointer library table
2016-01-28 Change pushbutton for a radially mounted button
    [power.sch, speedy.kicad_pcb, speedy.sch]
2016-01-29 Change micro USB connector & add 3d models to some footprints
    [speedy.kicad_pcb, speedy.sch]
2016-02-01 Replot schematic pdf for review
    [power.sch, sensors.sch, speedy.kicad_pcb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]
2016-02-02 Move SDIO pullups from clock to CMD
    see NXP AN10911 http://www.nxp.com/documents/application_note/AN10911.pdf
    [speedy.sch]
2016-02-02 Correct boot pattern to enable DFU
    Add a push button to VCC on Boot0 to accomplish pattern 1 from AN2606
    Previous configuration wouldn't have worked to trigger DFU as noted by @nuft
    [speedy.sch]
2016-02-19 Fix problems noted by @nuft during review
    - Force pulldown on unused bootloadr pins (USART 1 & 3)
    - Use one oscillator for both MCU and NRF
    [power.sch, sensors.sch, speedy.sch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]
2016-02-20 (Re)Place components on PCB
    Netlist was broken after review corrections
    Rebuilt and placed components from scratch
    [power.sch, speedy.kicad_pcb, speedy.sch]
2016-06-04 Update debug connector to use new CVRA convention
    SWD + UART connector using Molex picoblade 7pin connector
    [speedy.sch]
2016-06-04 Update TOF sensor to use new ST VL53L0X with 2m range
    [power.sch, sensors.sch, speedy.sch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]
2016-06-04 Update footprints/netlist
    [sensors.sch, speedy.sch]
2016-06-04 Update pdf schematic
    [power.sch, sensors.sch, speedy.sch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]
2016-06-05 Update form to square PCB, place components and update 3D models
    [speedy.kicad_pcb]
2016-06-23 Reorganise files
    [power.sch, sensors.sch, speedy.kicad_pcb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]
2016-06-25 Use wifi for telemetry
    Cleanup schematic
    Use ESP12E (wifi) for telemetry instead of NRF24
    Reannotate & replot pdf
    [power.sch, sensors.sch, speedy.sch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]
2016-06-25 Place components again after schematic update
    Increase size of board to 40mmx40mm
    [speedy.kicad_pcb]
2016-06-26 Update with small corrections
    Decrease LED resistor values
    Fix NUF2042 name
    Fix MPU9250 wiring (contradictory datasheet)
    [sensors.sch, speedy.kicad_pcb, speedy.sch]
2016-07-21 Finish routing
    [power.sch, speedy.kicad_pcb, speedy.sch]
2016-07-21 Plot gerber files
    [speedy-B.Cu.gbl, speedy-B.Mask.gbs, speedy-B.Paste.gbp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]
